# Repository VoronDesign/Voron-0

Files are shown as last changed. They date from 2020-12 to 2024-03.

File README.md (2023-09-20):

# Voron Zero

[**DOWNLOAD**](https://github.com/VoronDesign/Voron-0/archive/refs/heads/Voron0.2r1.zip)

Image of Voron Zero

The official release of the Voron Zero 3D printer. You can find the BOM in the configurator located at the [Voron Design]( http://vorondesign.com/voron0.2) website.

The current revision is **V0.2r1**

[**Printed Parts Guide**](https://docs.google.com/spreadsheets/d/1MSgTiXazJwyfcTe7QqNIMWwQ_lfM8cOXmiMWPZ2HkEI/copy)

## Highlights
- Compact and portable
- 120x120x120 build volume
- CoreXY
- Low mass direct drive extruder
- Enclosed chamber
- 24v DC bed
- Klipper firmware
- Filament runout sensor

## Release History

### V0.2r1 (2023 June)

**Skirts**
- We fixed the issue where 34mm Z motors didnt fit in the machine with the bottom panel installed, this involved increasing the height of the skirts/feet by 2mm
- We added a simple filament runout sensor to the rear right foot

**Toolhead**
- Mini Stealthburner direct drive and bowden cowling part cooling ducts improved 
- an issue with the guidler being able to pivot in an undesired direction was addressed by tightening the bolt holes to reduce play
- RIDGA support for the bearings that come stock with the ridga kit has been added

**Tophat**
- cam locks for the tophat were changed to a simple hex key design

**Z Endstop**
- z endstop mount was beefed up to improve ridgidity 

**BOM Changes**

the BOM increased by the following items
- 2x m2x10 self tapping screw
- 1x MR85 bearing
- 1x Microswitch
- 1x ECAS04 Bowden Collet

### V0.2 (2023 January)

A majority of the printed parts have changed. The configurator will give you an idea of parts needed if you are upgrading from V0.1.

**Toolhead**
- New design: Mini Stealthburner
- Direct Drive Extruder with BMG gears and 20mm thick pancake motor with 10 tooth spur gear
- Improved part cooling ducts (fans are same as V0.1)
- Supports Revo VORON, Dragon, Dragonfly BMO, DropEffect XG, Creality Spider Pro

**Drive units**
- Motor screw count reduction
- Endstop removed for sensorless homing

**Frame**
- No changes

**Tophat**
- All panels have changed
- All side panels are identical
- Extrusion based tophat
- Hinged design
- Cam locks to secure tophat in place

**Panels/Clips**
- All panels are 3mm
- Deck panel changed, new panel is not required
- Split rear panel

**X/Y Joints**
- Tops became 1mm smaller to accommodate MiniSB
- Endstop block removed for sensorless homing

**Bed Assembly**
- Printed parts changed, bed position moved 3mm to the rear

**Feet/Skirts**
- Trident skirt community mod folded into official release

**Front Idlers**
- Cam locks added

### V0.1 Inital release (2021 April)
See https://github.com/VoronDesign/Voron-0/releases/tag/V0.1

### V0.0 Updates and fixes (2020 Sept)
See https://github.com/VoronDesign/Voron-0/releases/tag/V0.0r1

### V0.0 Initial release (2020 April)
See https://github.com/VoronDesign/Voron-0/releases/tag/V0.0

Voron Logo

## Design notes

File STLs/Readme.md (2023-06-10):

You can Download the entire STL folder at once by clicking [**HERE**](https://download-directory.github.io/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)

# [Printed Parts Guide](https://docs.google.com/spreadsheets/d/1MSgTiXazJwyfcTe7QqNIMWwQ_lfM8cOXmiMWPZ2HkEI/copy)

This document lists all of the printed parts with images, names, and where they are used in the assembly manual as well as other helpful notes

# Part File Naming Guide

**QUANTITY REQUIRED**

*[a]_Thumb_Nut_x3.stl*  
Any file that ends with “_x#” is telling you the quantity of that part required to build the machine.

**BUILD SPECIFIC PARTS**

*SKR_E3_V3_Din_Mount.stl*  
Any file name that does **NOT** end with a quantity designation is a part that needs to be choosen based on the specific components and options you want for your build, things like controller boards, ADXL mounts or the Bowden toolhead are exampls of parts that will not have quantities and can be printed or not based on your choosing. 

**ACCENT COLOR**

*[a]_Tensioner_Knob_x2.stl*  
We have added “[a]” to the front of any STL file that is intended to be printed with accent color. The parts are marked with a heart in the manual when they first appear. 

**PRIMARY COLOR**

*B_Drive_Frame_Lower_x1.stl*  
These files will have nothing at the start of the filename.

**CLEAR / TRANSLUCENT**

*[c]_Display_Diffuser_x1.stl*  
Any file that begins with "[c]" is intended to be printed in a clear or translucent color that allows light to penetrate through it.

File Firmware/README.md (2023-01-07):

# Voron 0.1 Stock Printer Config Example

For detailed instructions on setting up your Voron, visit https://docs.vorondesign.com/build/startup/

As always, check Discord #voron_0_questions for help

## Quick Start

* Find and update your unique mcu `serial`
* Do a `STEPPER_BUZZ STEPPER=stepper_x` and repeat for each stepper
* Test each endstop using `QUERY_ENDSTOPS`
* Be ready to emergency stop, practice it
* Try homeing each axis, `G28 X` then `G28 X Y` then `G28`
* Adjust direction `dir_pin` as necessary
* Do a `BED_SCREWS_ADJUST` with the paper test
* Check fans are working properly
* Validate your thermistors `sensor_type`
* Tune bed `PID_CALIBRATE HEATER=heater_bed TARGET=100`
* Tune hotend with `M106 S64` then `PID_CALIBRATE HEATER=extruder TARGET=245`

## Warnings

* If using mainsail or others, you will likely need a special include or other adjustments
* You may need to swap your A/B motor physical connections and/or software stepper directions
* This firmware assumes stock BOM with Mini Stealthburner DD toolhead

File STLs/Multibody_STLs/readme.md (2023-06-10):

these Multibody STls are provided to make multi color printing of common parts such as the Cowling and skirts easier.

to use these STLs to print multi color parts import them into your slicer and split into parts (not objects) you can then use part specific settings to do things like color swaps or deleting top/bottom layer to make mesh skirts.

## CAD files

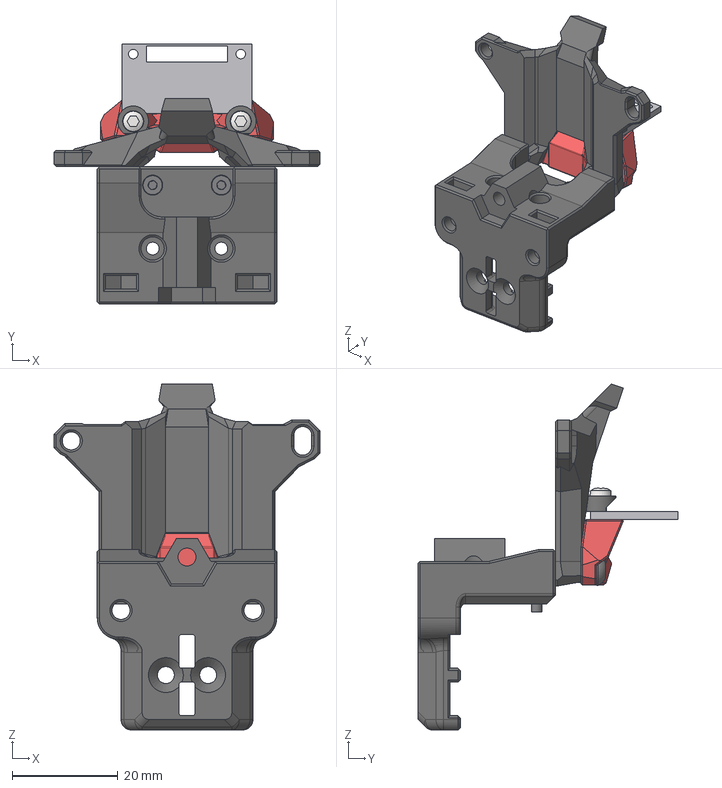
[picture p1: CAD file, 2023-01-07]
CAD/ADXL_Mounts/MiniSB_adxl_mount_adafruit_LIS3DH.step
50.3 x 49.2 x 65.5 mm
MiniSB_adxl_mount_adafruit_LIS3DH (1)
adxl_adafruit_LIS3DH
adxl_screw_spacer:1 (3) (1)
adxl_screw_spacer:2 (3) (1)
DIN EN ISO 7049 - ST2.2 x 6.5 - F - Z:1 (3)
DIN EN ISO 7049 - ST2.2 x 6.5 - F - Z:2 (3)
M3x12 BHCS (3)
X Carriage:1
Strain Relief Plate:1
M2x6 SHCS:2
M2x6 SHCS:3

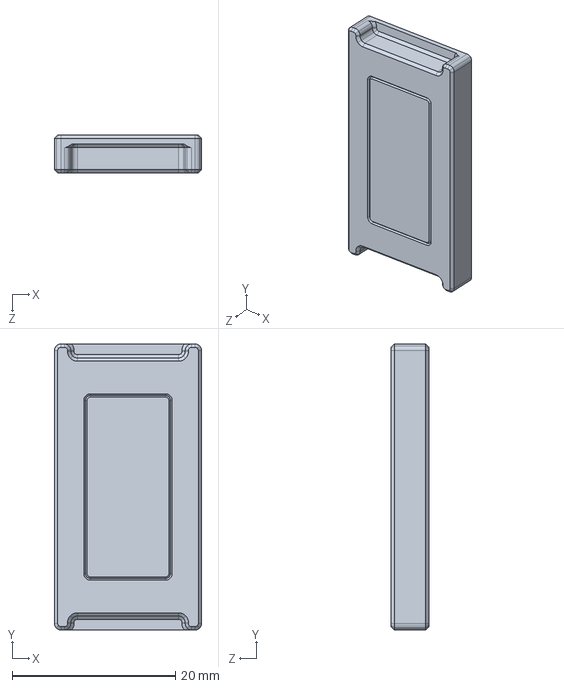
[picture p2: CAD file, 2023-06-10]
CAD/Electronics Mounts/VHB DIN Mount.STEP
18.0 x 35.0 x 4.60 mm

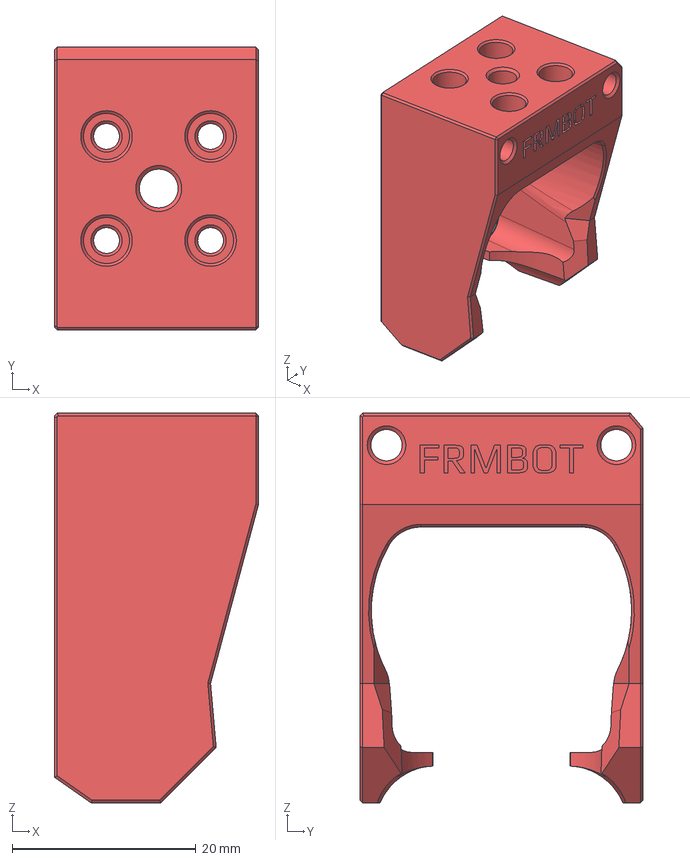
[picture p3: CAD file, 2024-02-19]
CAD/Hotend Mounts/Fan_Saver/FS_Hotend_Mount_Formbot.step
22.2 x 30.8 x 42.4 mm

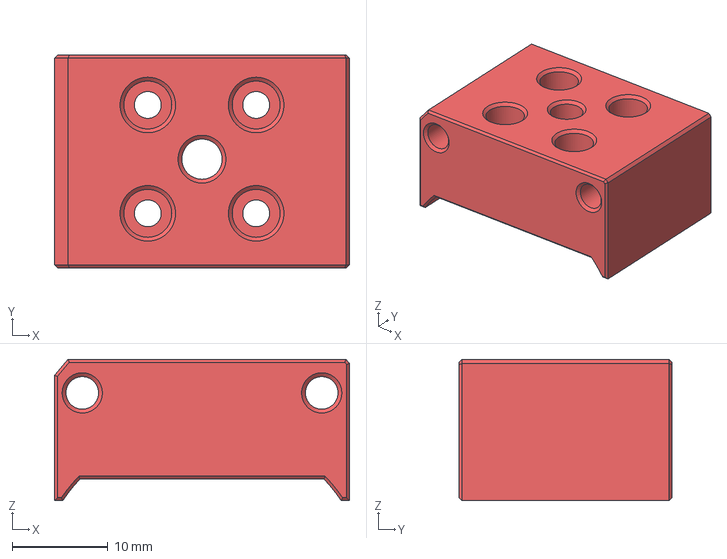
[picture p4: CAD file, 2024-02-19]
CAD/Hotend Mounts/Standard/Hotend_Mount_Formbot.step
30.8 x 22.2 x 14.7 mm

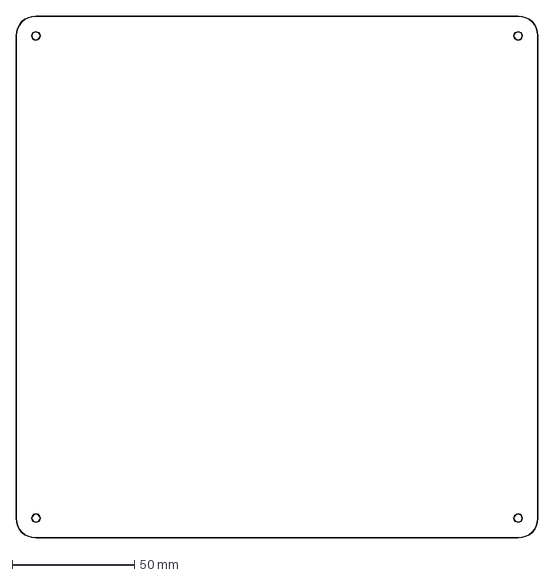
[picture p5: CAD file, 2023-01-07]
DXF/Bottom_Panel.dxf
213.0 x 213.0 mm

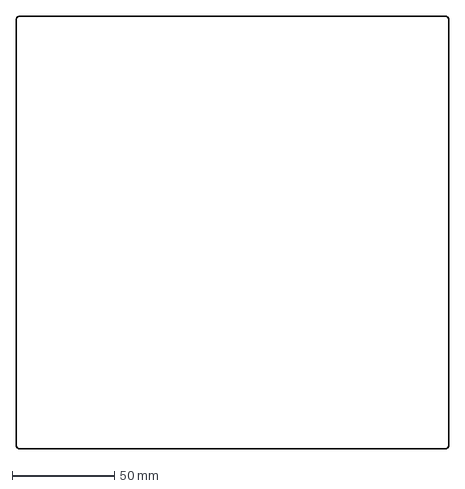
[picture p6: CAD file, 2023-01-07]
DXF/Tophat/Tophat_Top_Panel.dxf
212.0 x 212.0 mm

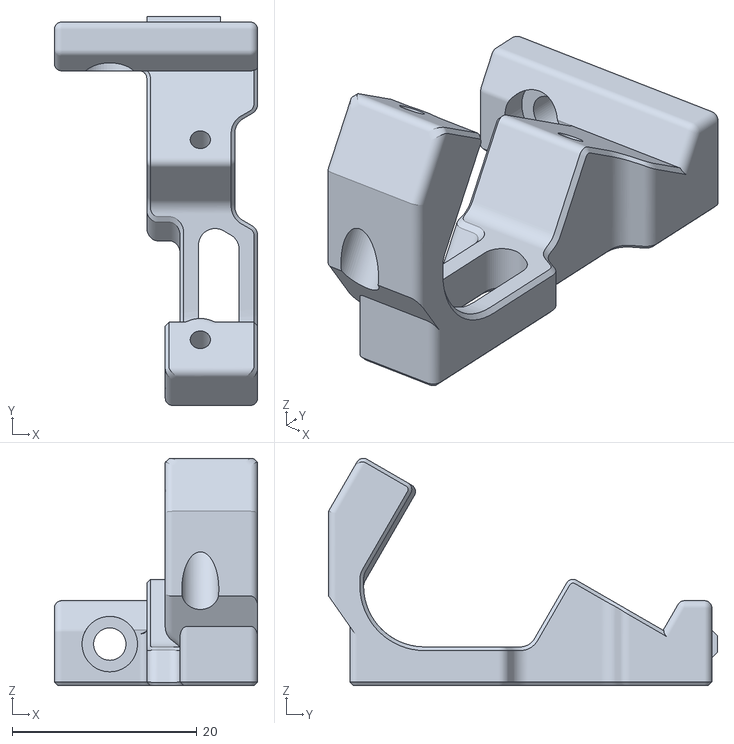
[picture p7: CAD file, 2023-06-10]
STLs/Display/Display_Mount_Right_x1.stl
22.0 x 42.1 x 24.6

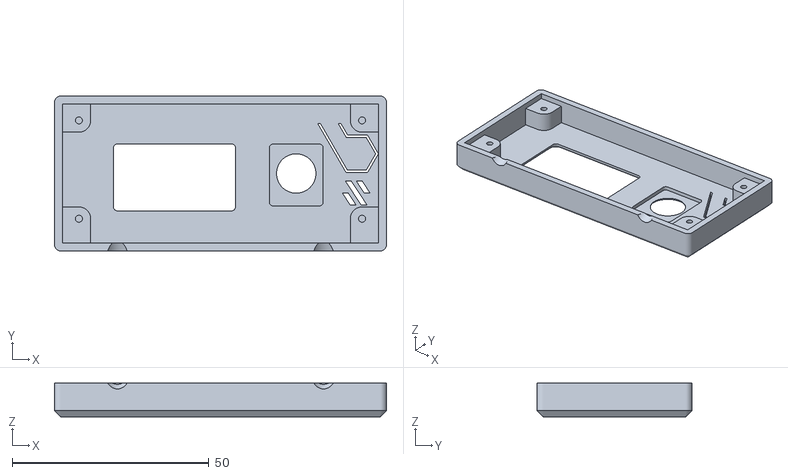
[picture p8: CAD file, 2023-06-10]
STLs/Multibody_STLs/Display/Display_Faceplate_Multibody_x1.stl
84.4 x 39.4 x 8.63

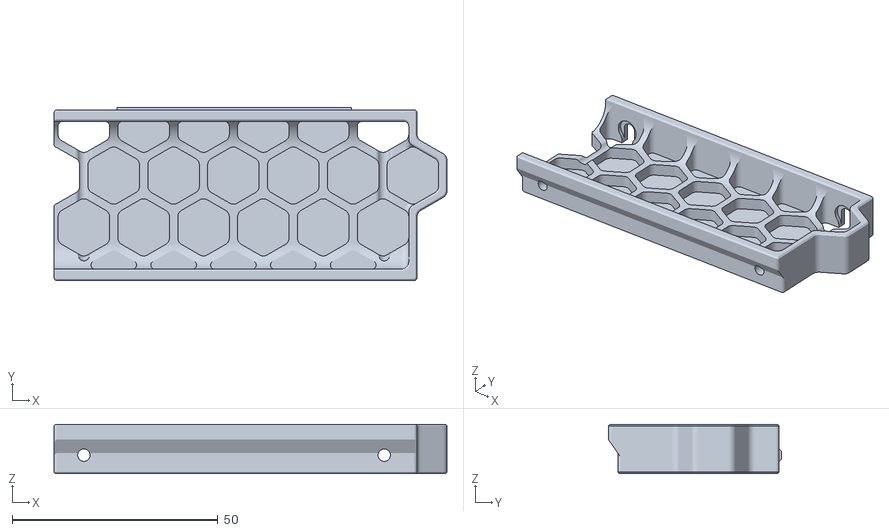
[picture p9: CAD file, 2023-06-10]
STLs/Multibody_STLs/Skirts/Side_Skirt_Mirror_Multibody_x2.stl
95.5 x 42.1 x 12.0

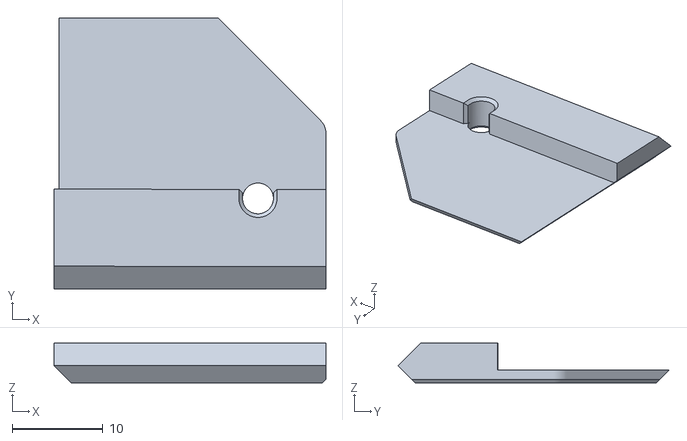
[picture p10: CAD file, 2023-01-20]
STLs/Panel_Mounting/Rear_Bottom_Left_Clip_x1.stl
30.0 x 29.9 x 4.40

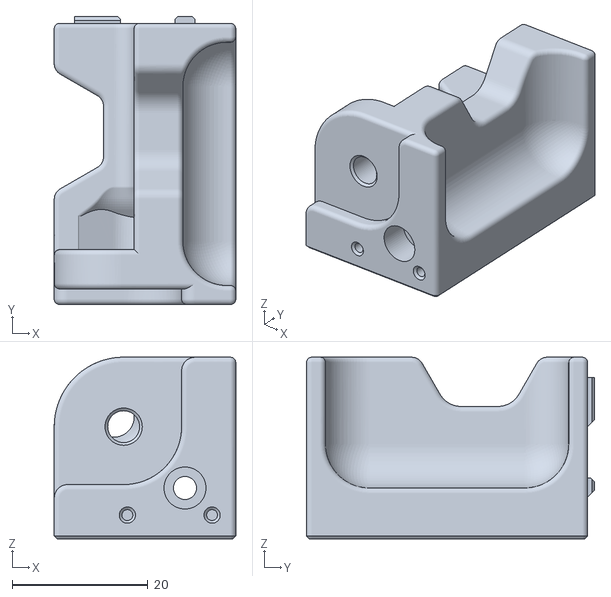
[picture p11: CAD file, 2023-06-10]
STLs/Skirts/Foot_Front_Right_x1.STL
26.8 x 42.5 x 26.8

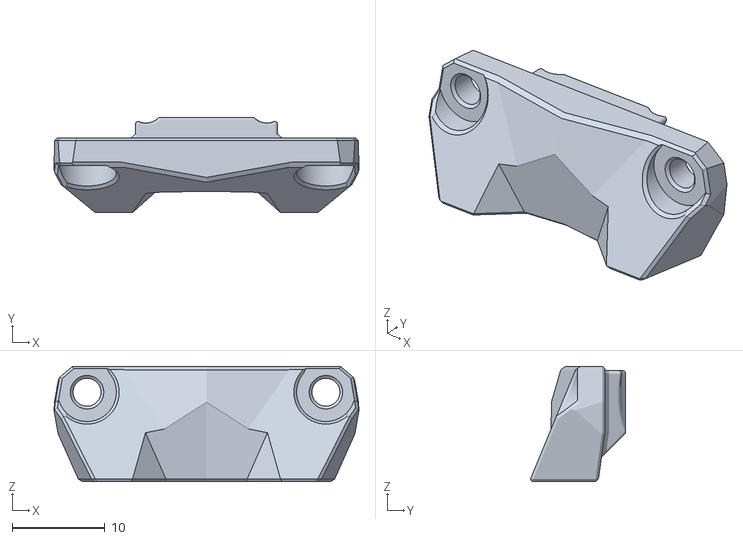
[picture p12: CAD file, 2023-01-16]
STLs/Toolheads/ADXL_Mounts/MiniSB_adxl_mount_generic_15.5mm.stl
32.8 x 10.3 x 12.4

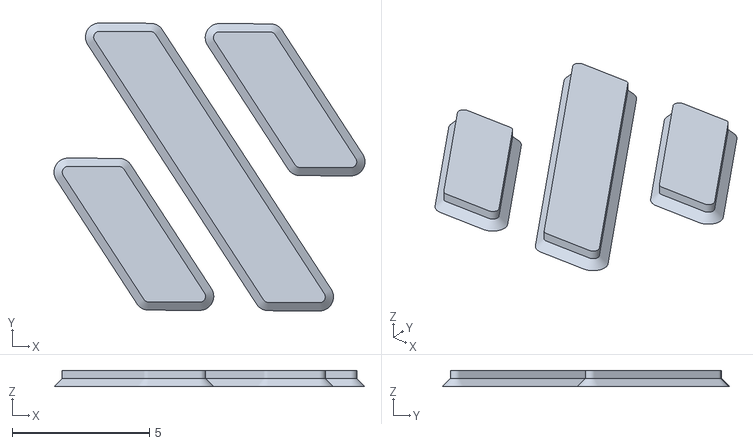
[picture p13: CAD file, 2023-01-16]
STLs/Toolheads/Bowden/MiniSB_Bowden_Logo_Insert.stl
11.3 x 10.5 x 0.6

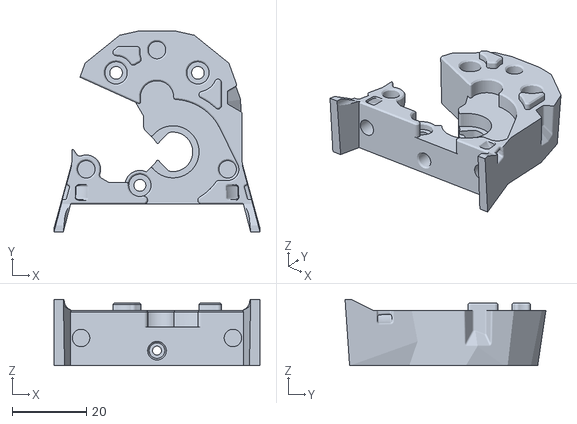
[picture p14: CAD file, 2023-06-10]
STLs/Toolheads/Mini_Stealthburner/[a]_MiniSB_MidBody_x1.STL
55.4 x 54.0 x 17.8

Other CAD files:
STLs/Electronics/VHB_DIN_Mount.STL
STLs/Toolheads/Hotend_Mounts/Fan_Saver/[a]_FS_Hotend_Mount_Formbot.stl
STLs/Toolheads/Hotend_Mounts/Standard/[a]_Hotend_Mount_Formbot.stl
STLs/Tools/Swiss_Army_Jig_x1.STL
CAD/ADXL_Mounts/MiniSB_adxl_mount_generic_15.5mm_c_c.step
CAD/ADXL_Mounts/MiniSB_adxl_mount_ldo_15mm_c_c.step
CAD/Electronics Mounts/Fly_Gemini_V2_Din_Mount_2pc.step
CAD/Electronics Mounts/Manta_M4P_Din_Mount_2pc.step
CAD/Electronics Mounts/RPi_or_BTT-Pico_Din_Mount.STEP
CAD/Electronics Mounts/SKR_3_Din_Mount.step
CAD/Electronics Mounts/SKR_3_EZ_Din_Mount.step
CAD/Hotend Mounts/Fan_Saver/FS_Hotend_Mount_Bambu_X1C.step
CAD/Hotend Mounts/Fan_Saver/FS_Hotend_Mount_Dragon.step
CAD/Hotend Mounts/Fan_Saver/FS_Hotend_Mount_Dragonfly_BMS_7_Fins.step
CAD/Hotend Mounts/Fan_Saver/FS_Hotend_Mount_Revo_Voron.step
CAD/Hotend Mounts/Standard/Hotend_Mount_Bambu_X1C.step
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

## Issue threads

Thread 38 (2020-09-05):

Gaps in Toolhead Blower Duct (Left)

mvrckcompany, 2020-09-05:
Thin walls around the screw holes on the part: "[a]_Toolhead_Blower_Duct_Left_TV6_x1" leads to gaps on the inside during slicing and printing. Attempted to alleviate the issue by enabling "Print Thin Walls" within Cura, to no avail.

Printed using recommended settings, please see attached for reference.

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

Roycinger, 2020-10-04:
I can confirm that S3D behaves in a similar fashion:
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

I'll have a try with SuperSlicer tomorrow

FHeilmann, 2020-10-19:
I checked back with the devs and they assured me that these holes do not impede the functionality of that part. Yes they are a little unsightly, but unfortunately the space around these featres does not permit a "fix" via thickening those sections.

I'm therefore going to close this issue. If you feel this has been in error and want to provide a rationale while this should be fixed apart from the visual aspect, feel free to reopen it!

Bests,
-Florian

FHeilmann, 2020-10-25:
@mvrckcompany the devs elected to fix your issue anyway. Latest master (with https://github.com/VoronDesign/Voron-0/pull/45 merged) should fix the slicing issue.

Closed 2020-10-19.

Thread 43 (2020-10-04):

Deck panel rear DXF missing segments

alatdneg, 2020-10-04:
I'm loading it into Freecad 0.18.4, and there are two curves missing, not sure if this is a FreeCAD bug or not, but the middle back plate loaded fine.

It's the two curves that connect the z-carriage inset.  --\\___/--

ta

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

Roycinger, 2020-10-04:
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

No issue for me here (QCad, Illustrator, Inkscape). Must be FreeCAD related

alatdneg, 2020-10-05:
Yup, FreeCAD seems to be a bit iffy on DXF's, I loaded it into Inkscape and re-exported as SVG, that loaded okay into FreeCAD.

I guess it might be nice if you included STLS of the plates at 3mm, 2.5mm  etc. As I imagine quite a few people would like to just print these, and it'd save them having to create the STL's from the DXF's which might be difficult for some people.

Closed 2020-10-05.

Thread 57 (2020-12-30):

Setup Guide Startup Pin No Serial Device

jgehrig, 2020-12-30:
The [Setup Guide](https://github.com/VoronDesign/Voron-0/blob/master/VORON-0/Manuals/V0_Setup_Guide.pdf) mentions setting `!PC13` on startup in the config. On my device with `!PC13` the serial port does not appear in `/dev` and no device is listed in `lsusb` either.

I resolved the issue above  by changing `!PC13` to `!PA14`. I suspect there was a hardware change in revision `V2.0`?

I'm not familiar with Klipper/SKR, and I can't find a good schematic to validate... Does this sound reasonable?

Upstream reference:
`https://github.com/KevinOConnor/klipper/issues/3461`

dubjay2k, 2020-12-30:
@jgehrig The SKR mini V2 does use a different pin than what's outlined in the setup guide (v1.2 specific).

It's mentioned in the V2 `printer.cfg` file, but should probably be mentioned in the setup guide as well.

https://github.com/VoronDesign/Voron-0/blob/74603b1752b24fcdebdb85c9d662b88075058e6f/VORON-0/Firmware/SKR_E3_Mini_2.0/printer.cfg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

raymondh2, 2021-02-12:
Closing due to inactivity

Closed 2021-02-12.

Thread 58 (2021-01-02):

Adjustment suggestions for the manual

Metti93, 2021-01-02:
Hello all
First of all I would like to say that I, a CAD designer, am very enthusiastic about this great printer. The parts, as well as the manuals and the community are of high quality and unparalleled.
That's why I want to use my skills as a quality manager and responsible for company standards in my company to make this great project even better. Starting with the manual!
When I assembled my V0, I felt a bit lost in certain parts of the manual.

**General hint:**
- That Loctite might react with ABS+ and might not be beneficial in certain places. A note on this might not be so bad, for noobs like me.
- I would make the text bubbles and their text larger. I'm not the youngest anymore, and would have liked more readable texts. Also, I'm not a fan of white text on an orange background.
- I would introduce a bubble/color for optional hints. Be it additional M3 nuts for future extensions etc..

**Page 6-7**
- I would number the profiles. Because I made the mistake of installing the wrong profile right at the beginning, which is what should be needed with the frame. Of course, I then simply added two holes. But that could have been avoided.

**Page 10-11**
- "2x" is not in the same place, on both sides!!!!! 😉

**Page 15**
- Bottom left illustration. Write on, nevertheless, please, that one puts a M3 nut under there in each case. I had wondered what it is held by, or if on any other pages this screw is used for something else, because it sits there loosely.

**Page 15-16**
- As an optional note, I would add additional M3 nuts lined with foam tape (thanks Christoph Müller#3576 for the tip).
Anyway, I would be happy if I had received such a tip early enough, and not only when I have assembled everything.

**Page 20**
- The title of the page is not aligned correctly.

**Page 25**
- A hint as to where the motor cable should look would be nice.

**Page 27**
- Backlash nut should be written on. Only at the end of the assembly, did I notice that this was missing. This was probably the worst thing missing from the manual.

**Page 29**
- Illustration at top left, "M3*6 BHCS + M3 Groove." Not that people use MakerBeam T-Nuts.

**Page 30**
- Foam tape would hold the nuts in place here, making it easier to mount the Z-motormount, but also the backpanel.

**Page 34**
- "M3*6 BHCS + M3 Nut."

**Page 35-36**
- M3 nuts, secured with foam tape, for future upgrades.

**Page 37**
- A measurement with the edge distance would be helpful, not that you tighten the rail in the completely wrong place already.
- Text "Use Rail Guides to Center Rail" is missing.

**Page 74**
- The M3 nuts on both sides of the rail should be listed, noticed they were missing on page 81. Had to take everything apart again.

**Page 136-137**
- The cable routing for the front fan, I would draw in better and route it through the notch for the left part fan.

For questions I am also available in Discord
All in all, it was fun to assemble the Voron.

mysfiring, 2021-01-15:
Didn't want to make a separate issue for a manual-related item: a callout on pg. 10 of the Pocketwatch manual - as a reminder to those using a non-spec motor - reminding the user that they should attach the 'pw_motor_spacer' at this point would be greatly appreciated! :D

nemgrea, 2021-02-20:
manual is getting re-made for v0.1 these issues will be taken into consideration and implemented where applicable

Closed 2021-02-20.

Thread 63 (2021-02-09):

Dragon Hotend Mounting

SneakyTiki, 2021-02-09:
The screws in the CAD are modeled as M2.5 x 12mm, but the stock Dragon Hotend (at least from Phaetus) comes with M2.5x8mm. The V0 BOM doesn't call for M2.5x12mm screws, and the Toolhead holes for mounting the hotend have 9mm of through depth :(

KoeRt888, 2021-02-09:
BOM calls for a V6 hotend, and I guess it only shows the BOM for this variant.
[Sourcing guide](https://vorondesign.com/sourcing_guide?model=V0) shows all hotend variants and contains the mention of the correct screws for the Dragon hotend.

raymondh2, 2021-02-10:
This is noted on the sourcing guide.

Closed 2021-02-10.

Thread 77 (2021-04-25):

BOM discrepancy?

bogeyf14, 2021-04-25:
BOM calls for "Bondtech Motor Gear" but it is unnecessary because the spec'd stepper already has a gear

VinnyCordeiro, 2021-04-25:
It is still necessary for those who opted for the bowden setup.

bogeyf14, 2021-04-25:
ok, I would recommend appending the description of that BOM line to say " Bondtech Motor Gear (required for bowden extruder)" or something to that effect. The manual doesn't show assembly of a bowden setup so it's not clear what this part is used for. I am sourcing parts for for the new toolhead and almost ordered this part because I didn't check the manual first, I doubt many other people will either.

raymondh2, 2021-04-25:
You are looking at two different versions of Voron zero

nemgrea, 2021-04-25:
issue fixed thanks for letting us know!

Closed 2021-04-25.

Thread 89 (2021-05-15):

Recommend revisions to V0.1 bed construction

fwiffo, 2021-05-15:
Having gone through a couple rebuilds of my bed, I'd like to offer a few suggestions for refinement:
1. Ditch the printed thumb knobs and go back to the knurled metal nuts from V0.0.
2. The Z adjustment screw hole strips out quickly. Thicker walls or something might help.
3. Put washers between the springs and lock nuts to keep them from getting cockeyed and buckling. I had a bad problem with mine shifting around on the nuts while adjusting. Adding a washer gave them a flat surface to push against.
4. Make the holes for the springs a bit shallower. That gives them a bit more tension at a given height making adjustments more reliable and gives a wider usable range.

nemgrea, 2021-05-20:
spec will stay with printed knobs for bom/cost reduction purposes. metal thumb nuts are still supported if users choose that route

im not sure what z adjustment holes would be stripping? we dont have any bolts threading into printed parts on z axis stuff

looking into adding the washers to help with the flat surface issue. this will require cad/manual updates

the hole depth for the springs is at its current depth to allow the full 120mm travel in z having the bed sit higher up may eat into this space. simply tightening the thumb nuts should compress the screw to whatever preload amount you would want. these parts will stay as modeled.

fwiffo, 2021-05-20:
I'm talking about the screw that hits the Z endstop switch (page 102 of the
manual).

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

--
Tom Schumm
http://www.fwiffo.com/

Megamannen, 2022-02-07:
Threading in plastic is really bad if you adjust it often. But I'm guessing this is a "set once or twice" for most users, in that regard it doesn't matter.

But the Voron is filled with threaded inserts, so what is one more?

staffert, 2022-02-09:
Simply using a second locknut would provide ample locking of the screw, or a brass heat insert with thread locking compound would be a better long term solution than simply a hole into plastic.

Closed 2022-08-04.

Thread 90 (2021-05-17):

20x5mm inlet fuse is missing from BOM

jarrettv, 2021-05-17:
These can be found at most hardware stores but it should be listed on BOM since you can't get going _safely_ without one.

DanJunior78, 2021-05-17:
Usually the inlets have a inlet fuse. Maybe a splitting between 220/110V heatbed to 24V power supply would make sense with 2 small 5A fuses

jarrettv, 2021-05-17:
I bought directly from digikey ala sourcing guide and it did not come with an inlet fuse.

DanJunior78, 2021-05-17:
Wow, usually they have a fuse coming with them. That's a usual size for inlets, even with a switch with light bulb.

nemgrea, 2021-05-18:
added

Closed 2021-05-18.

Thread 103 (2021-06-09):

Zip ties missing from BOM

grmocg, 2021-06-09:
Assembly requires zip ties in various locations, but they're not included in the BOM.

... And since some of the parts require smaller zip-ties than people are likely to have (smaller than 4in/100mm, which are typically the smallest in normal zip-tie assortments), it is worth a call-out somewhere like the BOM/sourcing guide!

nemgrea, 2021-06-11:
zip ties added to sourcing guide, thanks

samtny, 2021-06-21:
FWIW upon encountering this issue I grabbed these: https://www.amazon.com/dp/B0826Z1RLK

The quality is ... okay (minor burrs here and there), and my caliper says they are indeed 1.8mm width as described for the product.

tawera, 2021-07-08:
A suggestion for improvement: making the zip tie mount points compatible with 2.5mm would make sourcing easier. At least where I am from, I've checked many Swedish suppliers, all have 2.5mm, none have 1.8mm. And, incidentally, the ones that came with the prusa kit I bought were 2.5.

tme.eu has 1233 SKUs for zip ties, only 3 of which are 1.8mm or less, so these are rare...

Megamannen, 2022-01-15:
> A suggestion for improvement: making the zip tie mount points compatible with 2.5mm would make sourcing easier. At least where I am from, I've checked many Swedish suppliers, all have 2.5mm, none have 1.8mm. And, incidentally, the ones that came with the prusa kit I bought were 2.5.
>
> tme.eu has 1233 SKUs for zip ties, only 3 of which are 1.8mm or less, so these are rare...

Yeah, 1.8 is indeed a rare thing, here you have one (the only?) supplier though https://www.electrokit.com/produkt/buntband-71mm-x-1-8mm-svarta-100-st-panduit/

raymondh2, 2022-04-01:
Added to the BOM

Closed 2022-04-01.

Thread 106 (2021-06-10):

Wire length for x endstop is very tight

grmocg, 2021-06-10:
When wiring the V0.1, the suggest length of 400mm for the wire of the x-endstop seems a bit tight. Adding something like 20mm made it much more comfortable. Would be great to see a slightly longer length suggested!

grmocg, 2021-06-11:
Mounting the SKR after running this set of wires would make the lengths more reliably correct too, I suspect!

Closed 2021-06-14.

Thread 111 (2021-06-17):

Firmware/printer.cfg needs run current changes, too high for OMC Z-axis motors

KurioHonoo, 2021-06-17:
```
[tmc2209 stepper_z]
uart_pin: PC11
tx_pin: PC10
uart_address: 1
interpolate: True
run_current: 0.37       # For V0.1 spec NEMA17 w/ integrated lead screw
hold_current: 0.35
sense_resistor: 0.110
stealthchop_threshold: 500
```
The `run_current: 037` is fine for the LDO-42STH25-1004CL200E 1.0A, but is over the 0.28A max for the OMC 17LS13-0404E-200G 0.4A

Perhaps having two different configs in `[tmc2209 stepper_z]`, with the OMC being commented out by default, but adding additional commenting to inform the user.

I've added an example below as well as included all of the current BOM motors and their currents in case that information was helpful or if you wanted to incorporate them as comments into the config.

```
[tmc2209 stepper_z]
uart_pin: PC11
tx_pin: PC10
uart_address: 1
interpolate: True
#run_current: 0.37       # For V0.1 spec NEMA17 LDO-42STH25-1004CL200E 1.0A
#hold_current: 0.35
run_current: 0.2         # For V0.1 spec NEMA17 OMC 17LS13-0404E-200G 0.4A
hold_current: 0.15
sense_resistor: 0.110
stealthchop_threshold: 500
```

[tmc2209 stepper_x], [tmc2209 stepper_y]
OMC 14HS20-1504S 1.5A
LDO N/A

[tmc2209 stepper_z]
OMC 17LS13-0404E-200G 0.4A
LDO-42STH25-1004CL200E  1.0A

[tmc2209 extruder]
OMC 14HR07-1004VRN 1.0A
LDO-36STH17-1004AH 1.0A

hyperphonic0, 2021-06-19:
If you were going to have both configurations, it should probably the OMC motor that is uncommented by default because:
- The lower current setting of the OMC motor avoids any potential damage to the LDO motor, but the same is not necessarily true the other way around.
- The OMC motor is the _recommended_ motor in the sourcing guide, the LDO motor is the '_alternative source_'.

KurioHonoo, 2021-06-20:
I originally was going to say OMC too. Good point on it being the recommended one.

samtny, 2021-06-23:
Agree, choose the reasonably lower current as the default. My OMC was running super hot (2nd degree burn hot) before I caught this just now.

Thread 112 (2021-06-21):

Panel mounting clip STLs: incorrect part depth?

samtny, 2021-06-21:
About half the "3mm" set of panel clips have 5mm depth and fit my 3mm panel nicely, including room for VHB tape. The other half have 4mm depth and as a result have an awkward fit, requiring either loose tension of screws or some "flexing" of the clip to meet the rail.

The list of parts in the "3mm" set that have 4mm (perhaps incorrect?) depth is:

- 3mm_Bottom_Corner_Side_mirror_x1.stl
- 3mm_Bottom_Corner_Side_x2.stl
- 3mm_Middle_Clip_x9.stl
- 3mm_Top_Corner_Rear_mirror_x1.stl
- 3mm_Top_Corner_Rear_x1.stl
- 3mm_Top_Corner_Side_mirror_x1.stl
- 3mm_Top_Corner_Side_x2.stl

One way or the other, the fitment of the parts in this STL set seems to me inconsistent.

nemgrea, 2022-08-04:
this will be addressed with the v0.2 update

Closed 2022-08-04.

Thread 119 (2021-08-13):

Enclosing the high voltage compartment (bottom)

bmgoncu, 2021-08-13:
While the voron v0.1 is a great machine to tinker and build upon, there is a glaring safety issue of the exposed mains voltage compartment. The stock printer should include a solution where one can enclose the bottom with a 230mmx230mm acrylic sheet to keep fingers away whilst handling or moving the machine around.

For experienced users this may not be an issue but considering the popularity of this version  many novice tinkerers will build this printer.

nemgrea, 2021-08-16:
there are no exposed high voltage sources. psu terminals have a cover and all connections are spec'd to use correct fully insulated terminals. skirts also extend far enough down to prevent stray fingers from reaching the electrical cabinet.

it is never recommended to service or move the machine without first powering down the printer.

at the end of the day this is not a UL certified machine and it must be treated with a level of respect that any DIY mains voltage project would deserve.

Closed 2021-08-16.

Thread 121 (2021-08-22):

30mm blower fans sensitive to the hotend heat and stops working

bmgoncu, 2021-08-22:
The BOM specified GDSTime 30mm blower fans used for the Part cooling fans are susceptible to overheating from being in close proximity to the hotend.

Observed behaviour;
- When the hotend is hot the fan on the side of where the heater cartidge tip is visible, ossilates and doesnt spin
- When cooled down or when the hotend is not driven the fan spins as expected.
- The other part cooling fan spins normally.

Potential fixes;
- A not so temprature sensetive blower fan
- Somehow isolating the heat of the hotend from the fan hub.

Also asking for potential workarounds and/or solutions.

bmgoncu, 2021-08-23:
İ have done some further testing with a makeshift heat shield and it does appear to alleviate the problem. Havent tested with the chamber closed and heated but i think this is a good start;
https://youtube.com/shorts/RvsFIU7-kds?feature=share

https://youtu.be/qGwNJFiHI5k

bmgoncu, 2021-08-24:
Added the shielding with vhb to the fan (not ideal i know) the issue presides albeit the fan transitions to that state later (might be a placebo effect havent occured to measure the time).

bmgoncu, 2021-08-24:
More of the same issue i think;
https://discord.com/channels/460117602945990666/696930677161197640/877269535609212939

pfmooney, 2021-08-25:
Yep, I've seen this as well.  I even tried pushing the kickstart time up to 2s.  In a warm chamber, even 30% was too low for them to stay spinning sometimes, whereas 20% was fine cold.

pfmooney, 2021-08-28:
Al foil as a reflector does not appear to have helped at all.  I swapped the fan on one side for one of my spares and did not seem to help either.

lococnc, 2021-09-08:
Delta fans do not have this problem. My GDSTime fans lasted a day. Replaced and have no issues. Mine are 12v so it took adding a buck,

pfmooney, 2021-09-08:
> Delta fans do not have this problem. My GDSTime fans lasted a day. Replaced and have no issues. Mine are 12v so it took adding a buck,

That's for prints in a warm chamber, or in open air?

lococnc, 2021-09-08:
Sealed Chamber, printing ABS, I run fans 1t 16%

bmgoncu, 2021-09-08:
Can you provide an aliexpress link so i can verify? Maybe the BOM may change if it is indeed superior.

lococnc, 2021-09-08:
I bought from Digikey
https://www.digikey.com/en/products/detail/delta-electronics/BFB0312HA-A116/5022815
I used a small buck-converter to power the + terminal on fan, since the MCU switches ground.

blalor, 2021-09-08:
When talking fans, there’s little value in citing the brand or vendor as the sole detail. The DigiKey link is ideal. The useful info is in the specs, which are seldom provided on aliexpress, Amazon, etc. CFM, static pressure, voltage (obviously) and noise are all relevant.

lococnc, 2021-09-08:
Ali link to one identical to the ones I used.
https://www.aliexpress.com/item/1005003179503083.html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

Hexide, 2021-09-12:
Update on my insulation attempt:

After ~70 hours of printing, GDSTime fan started showing same failure symptoms. So issue was simply postponed rather than being fixed.

This calls for BOM fan to be changed to something that works better.

Personally, I will give a shot for listed Delta fan.

bmgoncu, 2021-09-12:
I already ordered a set, will arrive in 2 weeks i think. Will update with results.

xnaron, 2022-01-07:
@bmgoncu did the new fans work?  I noticed the Delta fan linked above is 12V.  Any issues with the airflow?  I guess it is better than a non spinning gdstime one :)

bmgoncu, 2022-01-07:
@xnaron yeah they totally do work, the airflow is signifocantly better (As it is the noise) and the best part no heat shielding at all (sorry for the radio scielence totally got carried away by other things and didnt report back)

xnaron, 2022-01-07:
@bmgoncu Awesome thanks!  Did you use a buck converter to get the 12V for them?

bmgoncu, 2022-01-07:
Actually no, i use the split wire config described in the doc

lococnc, 2022-01-08:
Buck it.

aschiweck, 2022-07-17:
> * Fan works fine when everything is cold
> * Fan maybe works for few layers if they are quick
> * Fan does not work by the end of print

I can confirm this issue also using a mosquito hotend.

I replaced the BOM specified GDSTime blower fans some time ago by ones from WINSINN, 30mm, Blower, 3010, Dual Ball Bearing, 24V. They are working smooth since then, regardless of heat or hotend state, no buck needed.

I bought them from [AmazonDE](https://www.amazon.de/gp/product/B08MKLDGQR/) but i think you can can get them also from https://winsinn.com/30mm-fan-raspberry-pi/ (3010 Blower - Dual Ball Bearing)

szafran81, 2022-12-10:
Both links from sourcing guide redirect to GDSTime fans (just checked).

Mstaniforth94, 2023-01-22:
I've recently been through about 6 of these fans, tried fan saver and this didn't help, and others on the Voron discord are still having issues with the fans on MiniSB.
https://discord.com/channels/460117602945990666/461210576618651669/1066792849221357578
Even with its new fan-saving design.

I have had one GDstine that's done 500+ hours and another do 20 minutes, 2 hours, 5 hours, 50 hours... on fully heat-soaked prints.

An inconsistent quality supplier is not a good quality one, with all the evidence and issues... I suggest these fans be removed from the BOM and the 5V Delta fans become the go-to. They may be double+ the price, but if that means you use less than double the fans over time, I think that's a better sourcing decision especially for newcomers just wanting to print stuff, and forcing the kit suppliers to send the better fans.

I did find cracking the door open stopped the issue on one of my GDstine fans, with fan saver too, but resulted in chamber temps cold enough to warp ASA on larger parts, thus meaning I was limited to ABS+ and small parts only.

szafran81, 2023-01-22:
My GDSTime did one Voron cube print, and after that they died each print after about 5mins.
Now I use the WINSINN 24V 3010 ones, and they work great.

porkcube, 2023-02-14:
Had GSTime 24V 3010 blowers on my 0.1, total failure of one in under 100hrs, replaced with Fabreeko upgrade kit and have almost 400hrs of them working fine since.

Separate new 0.2 build have been fighting the blowers, replaced right side 3 times before finally got a good cube out of ABS, then the left side started failing.   Tried fansaver and non-fansaver mounts which made no difference, only opening the door allows for a decent print with ABS.

Skystrike005, 2023-03-07:
I'm facing the same issue as well in miniSB. fan saver + dragonfly BMO lead to dead fans when the chamber is at printing temp. Fans are brand new, less than 1 hour of printing time.

Will try replacing the fans with winsinn ones. Heard they're much more stable. If all fails i'll try using dragon burner with 4010 fans.

nemgrea, 2023-03-16:
SG switched to winsinn fans mid feb. we'll try these for a bit. these are the fans i personally use in both v0's no failures yet.

danicedenv, 2023-03-20:
@nemgrea did you see any relevant dip in cooling performance? I ordered some Winsinn fans because my GDSTimes can't keep up with the heat. I am only hesitant because as far as I understand they don't push as much air and I mostly print PLA. Then again I don't want to give up being able to print ABS properly.

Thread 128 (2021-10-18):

Incorrect Stealthchop Setting in the Default Config

hyperphonic0, 2021-10-18:
There is quite a lot of discussion on Discord right now, with people having problems with the wrong default setting in the repo.  This has lead to many turning off Stealthchop entirely, meaning they will not benefit from near-silent - _and skip free_ - steppers.

[Klipper docs](https://www.klipper3d.org/TMC_Drivers.html) are fairly clear that Stealthchop should either be always on, or always off:

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

So I would suggest changing the default configuration for `stepper_x`, `stepper_y` and `stepper_z` to:

`stealthchop_threshold: 999999        # Comment out to turn off StealthChop`

I doubt that using Stealthchop on the extruder motor is going to provide any benefit, and because it can reduce the motor torque at higher speed it may cause problems. I would suggest turning it off for the extruder.

Stephan3, 2021-10-18:
https://github.com/Klipper3d/klipper/blob/5c10001bc525701f0ef004041cbbf093522f6de6/klippy/extras/tmc.py#L512

Take a look at the code. If value is 0, pwm mode is false and therefor the field in the register is too.
With a value of 0 stealtchop is disabled.

hyperphonic0, 2021-10-18:
I'm not quite sure what you're saying, but I'm suggesting the default config should have Stealthchop turned on by default, with the included comment explaining how Stealthchop can be turned off, if that is what is desired.

I believe setting `stealthchop_threshold: 0` would also turn it off, as would excluding the setting from the config.

samtny, 2021-10-21:
lol, i put a PR in for the extruder one, didn't see this issue:

https://github.com/VoronDesign/Voron-0/pull/127

#127

PR turns off stealthchop on the extruder only. I have personally troubleshot this with at least five people in the discord since I built my V0.1, July-ish.

hyperphonic0, 2021-11-02:
@nemgrea not sure why this was closed, #127 doesn't resolve this issue, it turns Stealthchop off for the extruder but does nothing the A/B drives or Z axis.

I think my original suggestion is still correct. I can create a pull request if you’d prefer, but thought an initial discussion here would be a better point of reference; It can be a bit difficult to discuss this kind of issue on Discord!

Closed 2021-10-31.

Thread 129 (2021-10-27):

Manual: Move mention of nut usage

newphreak, 2021-10-27:
On page 16 in the manual you're told to install the rail stoppers, but there's no mention of nuts being shown before page 18. Makes more sense to mention it the first place you use them. Props to setyte#5616 @ discord

HitLuca, 2022-12-30:
I also encountered this issue. A first timer may assume that they need to be screwed directly to the extrusion, which wouldn't be possible. Moving the note from page 18 to page 16 would easily fix the issue

Closed 2023-01-08.

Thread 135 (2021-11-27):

Problem in Downloading some .stl´s

klotzii-vr6, 2021-11-27:
There is a problem in downloading the following .stl´s:

- PSU_cover_x1.stl
- Power_Inlet_x1.stl
- Raspberry_Pi_3b_Mount_x1.stl
- Rear_Bed_Mount_Left_x1.stl
- Rear_Bed_Mount_Right_x1.stl

Can´t download them because after a click on the download button, it opens the file as a txt-file.
PSU_cover_x1.stl doesn´t even offer a download button

heizie, 2021-11-29:
try to use `git clone`

raymondh2, 2021-12-17:
Right click the text and save as.

raymondh2, 2021-12-17:
As for the ones without a download button click raw then do the same

Closed 2021-12-17.

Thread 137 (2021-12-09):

PrusaSlicer Profile extrusion width

gsezz, 2021-12-09:
The extrusion width percentages in the PrusaSlicer profile seem to be based on Nozzle diameter, like SuperSlicer does.
PrusaSlicer calculates them on Layer height.

raymondh2, 2021-12-18:
I'm not entirely sure what you are asking. Are you refering to the one build into Prusa Slicer? If so we don't maintain that.

gsezz, 2021-12-18:
No, I'm refering to the [VoronV0.ini](https://github.com/VoronDesign/Voron-0/blob/Voron0.1/Slicer_Profiles/PrusaSlicer/VoronV0.ini) here on github. For my Understanding, it's supposed to work with Prusa Slicer. But `extrusion_width = 110%` doesn't make much sense in Prusa Slicer, since it bases percentages on Layer height, not on Nozzle diameter, linke Super Slicer does. So while 110% sounds reasonable for Super Slicer (0.44mm extrusion width with a 0.4mm nozzle), this setting would lead to 0.22mm in Prusa Slicer (based on 0.2mm layer height).

nemgrea, 2022-01-05:
fixed

Closed 2022-01-05.

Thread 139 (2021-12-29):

5V Hot End Fan in to 24V FAN0

SanderRave, 2021-12-29:
Hi team,
I crossed this discrepancy by accident while searching for configuration info in Voron Documentation under Voron V0.0 - SKR mini E3 V2.0 Wiring: https://docs.vorondesign.com/build/electrical/v0_miniE3_v20_wiring.html#voron-v00---skr-mini-e3-v20-wiring

Bulit 4; Plug Hot End Fan in to FAN0 (pin PC6), is FAN1 (pin PC7) in the example Github printer.cfg: https://github.com/VoronDesign/Voron-0/commit/fa6f00e1f4592a6e5fb8976414297ccbbb6d4b64
Both pins have 24V output.

However, in the Voron sourcing guide, a 3007 axial fan 5V (min 3.5CFM) is specked: https://vorondesign.com/sourcing_guide
Connecting the fan straight to FAN0 or FAN1 will fry your hot end fan. With a lack of +5V outputs, my positive is wired to the probe +5V pin and FAN1 ground. Not sure where that wisdom came from, but I didn't make it up by myself.

Hope this helps making future building experiences even more awesome!

alvius, 2021-12-30:
You are looking at v0.0 documentation and v0.1 BOM. Check v0.0 BOM or v0.1 documentation.

raymondh2, 2021-12-30:
Closing as the referenced docs are not for the correct revision of Voron Zero

Closed 2021-12-30.

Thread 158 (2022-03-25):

Mosquito_Toolhead_DD for 3007 BOM fan

beaugalbraith, 2022-03-25:
Hey there,
Is it possible to create a MiniAfterburner toolhead for the Mosquito hotend using the 3007 fan? I printed the Mosquito toolhead. it appears to have been designed for use with a 25mm fan mounted directly to the heatsink. The other toolheads are designed for use with the 3007 fan seated inside the cowling.

If you look at the toolheads stls you can quickly see that the Mosquito version doesn't have the notch cutout, at the top, that the other toolheads have.

Thanks
-Beau

hyperphonic0, 2022-03-25:
Try this:

https://github.com/hyperphonic0/VoronMods/blob/main/V0.1_Mosquito_Cowling_with_3007_Fan.STL

raymondh2, 2022-03-25:
The toolhead is designed for the 2510 fan intentionally.

Closed 2022-03-25.

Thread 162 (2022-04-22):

Necessary part for bowden setup missing in V0.1 release

ianbruene, 2022-04-22:
The parts for a bowden toolhead are present, and the assembly manual does acknowledge that a bowden setup is possible even if it does not explain how to assemble it. However the belt retention block is not included in the V0.1 release. I had to dig up the previous V0.0 release to find the part.

If the bowden is deprecated to the point that parts can be dropped, then they all need to be dropped to avoid confusion. Alternatively if the option for a bowden setup is retained people need all of the parts for it.

Suggested fix: add belt retention block STL to the bowden toolhead directory.

nemgrea, 2022-04-22:
addressed by PR #163

Closed 2022-04-22.

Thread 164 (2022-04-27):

Manual: Change Z endstop trigger screw to SHCS from BHCS

Kozova1, 2022-04-27:
This screw on the T-nut block that is used for hitting the Z endstop is currently a BHCS.
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
It causes inconsistent endstop triggering and thus should be changed to be a slightly shorter (maybe M3x10?) SHCS screw.

raymondh2, 2022-04-27:
What do you mean inconsitent triggering? Between prints or when testing the endstop?

Kozova1, 2022-04-27:
Both - what happens is that sometimes I try to home and it crashes into the bed sometimes

nemgrea, 2022-08-04:
the screw is inline with the switch, changing to a larger hex head will cause more inconsistency as there is less contact area, refer to the cad for a better understanding of what im describing

Closed 2022-08-04.

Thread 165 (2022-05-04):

End of chain link attachment instructions is missing.

jbeougher7924, 2022-05-04:
Page 90 END LINK? WHAT END LINK?
The end piece of the chain was attached in an earlier step.
If you missed the installation you may be able to mount it to the outside.
A printed cable chain with a small bend radius is included in the released files

However on page 29 shows the end of chain is attached to the bed, however there are not instructions on how to do this.  Page 27 shows the same image but with out the chain link.  The instruction on page 90 are wrong since there is no instruction on attaching this to the bed.  Let alone that brass inserts are needed as well to attach the link to the bed.

ChrisN90, 2022-05-04:
It's not very clear in the manual but it is on page 13 under 'component prep'.

jbeougher7924, 2022-05-04:
Might want to clarify this page better and explain what needs to be done.  Align the page like the other pages.

Closed 2022-07-25.

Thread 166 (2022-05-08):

Manual: some issues I encountered on my build

atlaste, 2022-05-08:
First off, nice work! I really enjoyed assembling my machine using a PIF kit, and am eager to start printing with it. During assembly, I kept note of the issues I encountered, in the good spirit of open source sharing. I only encountered a few issues; hope it helps.

Issues I had with assembly:

1. Not really had an issue with this, but on page 59 it would be nice to say that the notches of the anti backlash nut should match up, so that they the nut stays on tension.
2. Page 64 should make a note about the rotation of the stepper. The kit I had (Fysetc) has the wires cut to the right length, so the connector for the cable should be pointed towards the back of the machine. This is a more general remark btw; I would have liked to know what the rotation was of the A/B stepper as well; during assembly I assumed the cables should go to the back instead of to the sides, which was wrong (and had to fix it later).
3. Screws that implicitly tap the plastic will destroy the plastic if it's not made to very tight tolerances. I found out the hard way while mounting the pcb brackets (crack...), and manually ran an m3 tap and a 1.5mm bit through the plastic to fix the issue (that's page 128 and 149).
4. Preload 4 nuts for the door handle magnet triangles. Page 38 I suppose, page 150 uses them. It's quite painful to add them later...
5. Belt tension on page 86 is hard to get right without some reference. Is it perhaps possible to use a phone and check the belt frequency?
6. Page 101 with the Z end stop. I just loosely put the nuts on the screws, and then fix them once they are in place. No need to drop them and fight gravity.
7. Page 108 apparently has a different PTFE length than I needed. I needed a total length of 30mm. I would perhaps note that the exact length is very important here; I cut it at 30.2mm at first, and to my surprise it was binding at page 114 because it was 0.2mm too long. It also seemed important to me to cut it with a sharp knife to ensure that the inner size is not smaller than it should be.
8. Getting those fans in place is terrible to get right... Pfew.
9. My thumb screw at page 116 has a separate spring which isn't noted. Feels quite tight. It does appear on the drawing.

That's it. As I said, nothing much for such a detailed design and manual. Hope it helps!

Cheers,
Stefan.

vavaroutsos, 2022-09-15:
I'll add a couple of more issues I had.

1) The lower cable chain end should be mounted to the extrusion using the top hole, not bottom. If you use the bottom hole, the top of the cable chain is a bit too high when the build plate is at Z=0 and it gets caught behind the gantry when moving towards Y=120.

2) The position in the manual for the Z guide rails seems at least 2mm too high. I had about 2mm of rail above the carriages when Z=0 (build plate thumb screws as tight as possible). This didn't allow me to get a full 120mm of Z travel.

3) The left/right position of the Z stage extrusions is critical for some build plates. The PEI spring steel I got with my LDO kit was slightly smaller than 120x120mm. This means any left/right shift in the build plate position (due to extrusion/rail location) takes away from usable build area. I lost a little over 1mm due to my build plate not being perfectly centered. This would not be an issue if the PEI spring steel were oversized 130x130mm.

HitLuca, 2022-12-30:
I took the feedback from @atlaste and updated the manual with some very simple annotations. @vavaroutsos , if you could give me the exact locations of the issues/tips you encountered I will update it with your suggestions as well.
I also added a note on which thread locker to use, as well as integrating the tip on cable routing from [this comment](https://github.com/VoronDesign/Voron-0/issues/176#issuecomment-1325972974)

Keep in mind it's a 5 minutes job and I hope it will be made obsolete by an update to the manual. I also had to compress it since the max file size is 25/26MB and the manual is 27 -.-

[Assembly_Manual_0.1_compressed.pdf](https://github.com/VoronDesign/Voron-0/files/10325070/Assembly_Manual_0.1_compressed.pdf)

vavaroutsos, 2022-12-30:
Referring to my previous comment:

1.	Page 36
2.	Page 18
3.	No page, probably an issue with the counter bore depth on the thicker LDO build plate.
4.	Page 25

Regards,

Pete

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

nemgrea, 2022-12-30:
we wont be making updates to the v0.1 manual anymore, we are focusing on the v0.2 manual which incorporates everything you have all mentioned here. thank you for the feedback.

HitLuca, 2022-12-30:
Well that's great news! Looking forward to see what the 0.2 improvements are :)

Anacardium12, 2022-12-30:
Is there already a known release date for the V0.2?

raymondh2, 2022-12-30:
There is no announced release date.

Closed 2023-01-08.

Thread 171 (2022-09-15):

BTT SKR mini E3 v2.0

vavaroutsos, 2022-09-15:
Can we remove this board from the sourcing guide/manual and replace it with something else? The SKR mini E3 v2.0 has no transient protection for the fan driver MOSFETs. The MOSFETs are rated at 30V which is easily exceeded by inductive switching spikes when the fan is turned off. This causes the body diode to go into avalanche break down. The MOSFETs are not designed to be operated this way and it's very poor practice. There are many threads on discord, reddit, github, etc. about fan failure on these boards.

The SKR mini E3 **v3.0** board has added flyback diodes to clamp spikes when switching inductive loads. The v3.0 board also has much better heat sinks and a 3rd fan output. The BTT SKR pico also has flyback diode protection for the three fan output MOSFETs, has a good heatsink, and is RPi form factor so it can be stacked..

nemgrea, 2022-09-18:
no further changes will be getting pushed for the v0.1 all efforts are now being placed on development for the v0.2 release which will not include the v2 skr board

Closed 2022-09-18.

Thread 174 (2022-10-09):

MidBody PTFE hole not deep enough.

paledrak, 2022-10-09:
It appears that on the STL for the [a]_Mid_Body_Revo_Voron_x1.stl has an error. The PTFE tube hole is only about 1mm deep and the PTFE tube does not sit securely in the Mid Body. The other tool head mid bodies have this hole much deeper.

It this by design or does the model need to be modified?

nemgrea, 2022-10-10:
this is by design, if the ptfe goes deep into BOTH the mid body AND the hotend then you will not beable to install the two components as the hotend needs to be installed and screws tightened before the mid body can be installed and it need to be slid into the assembly in a manor that would not allow 8mm of ptfe to be inserted at that stage.

so yes its done on purpose to aid in the assembly of the toolhead.

both the revo voron and the dragonfly BMO hotend require this smaller counterbore mid body.

Closed 2022-10-10.

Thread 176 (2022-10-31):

Manual Missing Critical Step

suprchunk, 2022-10-31:
Page 96 shows the installation of the cable chain. It shows the correct mounting for the top to the bed mount. It does not show it being attached to the bottom. It should show this. That is problem 1.

Problem 2: it doesn't mention shortening the chain to ensure that the y-stop isn't triggered/broken or whatever will happen when the bed is raised an one is no longer able to zero the machine.

The cable chain is obviously in need of shortening, however one does not realize this until the machine is constructed already.

There is also a need to rewrite the manual, as a lot of information is missing, not touched on, or somehow assumed. Just mentioning this one issue that I ran into that causes a serious issue; unless blocking a stop, or setting it off prematurely is intended.

nemgrea, 2022-11-01:
installation of the other end is shown on page 36.

the length of your chain depends on the supplier that you buy that item from. we will consider adding a note to the next revision.

> as a lot of information is missing, not touched on, or somehow assumed

if you have specific things you struggled with that would be helpful...general statements like this dont do us much good though if we dont know whats missing we dont know what to add...

eadz, 2022-11-24:
Personally I found the manual was a bit of an IQ test with puzzles to fill in the missing information in places.

Two things I did wrong, that were not explicitly mentioned in the manual:

Orientation of the plug for the A B motors  - the diagrams do not show this anywhere. Turns out the plugs need to face inwards. I had to redo this part.

The second thing is the wiring of the hot end wires, and how they go down through the gap between the z rails before going under the mentioned side gap. on page 91 there are two highlighted cable paths, but I believe that the cables also need to run through the gap at the back of the head bed?

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

Overall though, a pretty fantastic achievement to make a manual that can build a complex printer with an Ikea-style manual!

Closed 2023-01-08.

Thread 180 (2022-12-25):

Shift layers problem help

sima35, 2022-12-25:
Good, I have one problem ,that I can't solve even after several settings.
I set mechanically and klipper.
The problem is that for an unclear reason, the layer is moved.
The belt is stretched accurately.
Speed from 50-100, I don't use a higher speed.
I have it set stealthchop_threshold: 999999. I had it set to 250 and it was even worse.
I have the printer settings below.
Thanks in advance for all the help

[stepper_x]
step_pin: PC0
dir_pin: PC1
enable_pin: !PA8
rotation_distance: 40
microsteps: 16
full_steps_per_rotation: 200
endstop_pin: ^PB4
position_endstop: 120
position_max: 120
homing_speed: 85

[tmc2209 stepper_x]
uart_pin: PA3
tx_pin: PA2
uart_address: 0
run_current: 0.850
hold_current: 0.770
stealthchop_threshold: 999999

[stepper_y]
step_pin: PC14
dir_pin: PC13
enable_pin: !PC15
rotation_distance: 40
microsteps: 16
full_steps_per_rotation: 200
endstop_pin: ^PC8
position_endstop: 120
position_max: 120
homing_speed: 85
homing_retract_dist: 5
homing_positive_dir: true

[tmc2209 stepper_y]
uart_pin: PA3
tx_pin: PA2
uart_address: 2
run_current: 0.850
hold_current: 0.770
stealthchop_threshold: 999999

[stepper_z]
step_pin: PB9
dir_pin: !PB8
enable_pin: !PC2
rotation_distance: 8
microsteps: 16
full_steps_per_rotation: 200
endstop_pin: ^PB1
#position_endstop: 0
position_max: 120
position_min: -0.290

[tmc2209 stepper_z]
uart_pin: PA3
tx_pin: PA2
uart_address: 1
run_current: 0.350
hold_current: 0.300
stealthchop_threshold: 5

[extruder]
step_pin: PB2
dir_pin: PA15
enable_pin: !PD2
rotation_distance: 4.333
microsteps: 16
full_steps_per_rotation: 200
nozzle_diameter: 0.400
filament_diameter: 1.750
heater_pin: PC6
sensor_type: EPCOS 100K B57560G104F
sensor_pin: PC4
#control: pid
#pid_kp: 21.527
#pid_ki: 1.063
#pid_kd: 108.982
min_temp: 0
max_temp: 270

[tmc2209 extruder]
uart_pin: PA3
tx_pin: PA2
uart_address: 3
run_current: 0.320
hold_current: 0.280
stealthchop_threshold: 5

[heater_bed]
heater_pin: PC7
sensor_type: EPCOS 100K B57560G104F
sensor_pin: PC5
#control: pid
#pid_kp: 54.027
#pid_ki: 0.770
#pid_kd: 948.182
min_temp: 0
max_temp: 115

#fan for printed model FAN0
[fan]
pin: PA14

#fan for hotend FAN1
[heater_fan my_nozzle_fan]
pin: PA13

[temperature_sensor raspberry_pi]
sensor_type: temperature_host
min_temp: 10
max_temp: 100

#[temperature_sensor mcu_temp]
#sensor_type: temperature_mcu
#min_temp: 10
#max_temp: 100

[printer]
kinematics: corexy
max_velocity: 200
max_accel: 2100
max_z_velocity: 5
max_z_accel: 100

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

raymondh2, 2022-12-25:
Hello! We primary use GitHub for managing design issues and not printer support. I would recommend seeking support on our other platforms listed below.

Reddit: https://www.reddit.com/r/vorondesign/
Discord: https://discord.gg/voron
Forum: https://forum.vorondesign.com/

Closed 2022-12-25.

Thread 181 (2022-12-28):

[temperature_sensor mcu_temp]

sima35, 2022-12-28:
Can you help me, I have a temp problem for mcu in klipper.
If I approve the code for mcu temp in klipper it shows an error.
MCU 'mcu' error during config: Not a valid ADC pin
Once the underlying issue is corrected, use the
"FIRMWARE_RESTART" command to reset the firmware, reload the
config, and restart the host software.
Error configuring printer

sensor_type: temperature_mcu
min_temp: 0
max_temp: 100

timmit99, 2022-12-28:
For issues like this please use the Discord. Github issues for issues with the  files shown here.

Closed 2022-12-28.

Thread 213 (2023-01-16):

Why is there no support for the Mosquito hotend?

green-forg, 2023-01-16:
Just simply out of curiosity, why there is no support for the Mosquito hotend? Is this because of mechanical issues or something else? Sincerely look forward to any replay, and appreciate your guys' contribution.

nemgrea, 2023-01-16:
because i didnt want to make a mount for it.
I have no idea if it works or has issues as it was never tested with the new toolhead by the dev team.
the cad is available so anyone is free to make their own mosquito mount.

hyperphonic0, 2023-01-16:
@green-forg Here you go, it works great (so far) on the Mini Stealthburner.
Use the longer 2.5mm fan screws through the face with 'Mosquito' written on it for added stability.

[Hotend_Mount_Mosquito.stl.zip](https://github.com/VoronDesign/Voron-0/files/10427937/Hotend_Mount_Mosquito.stl.zip)

green-forg, 2023-01-17:
Wow! That's nice! Thank you for your replay!

Closed 2023-01-16.

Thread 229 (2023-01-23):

CAD different to STL's

MugenMicko, 2023-01-23:
Hotend Mounts don't have air ducting attached as per the CAD. Also, there is a fitment issue between the CAD Hotend mount with ducting and fitment to the Front Cowling. May need CAD updating

nemgrea, 2023-01-23:
hotend mounts with the "air ducting" are under the fansaver folder.

can you elaborate on what the fitment issue you are seeing in CAD is please?

MugenMicko, 2023-01-24:
I apologise, appears to have been rectified with a previous CAD update, my bad.

Closed 2023-01-24.

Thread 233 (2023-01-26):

Assembly Manual Correction

meistertek, 2023-01-26:
Page 27 Assembly Balloon "Preload 2 M3 Nuts" needs to be re-worded (Preload 4 M3 Nuts and screws) and needs a second circle end leader (multi-leader) pointing to the middle of the Top Extrusion. This will prevent people from missing that a total of 4 M3 Nuts are needed in this sub-assembly.

nemgrea, 2023-01-26:
i dont believe there are any other components that get added to that extrusion?

the preload nuts currently being referenced are for the Z_Motor_Mount to attach to

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

nemgrea, 2023-02-08:
Closing due to no response

Closed 2023-02-08.

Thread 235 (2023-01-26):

Rapido

Rajonex, 2023-01-26:
Hello,

What is the reason why Rapido mount is missing, but MicroSwiss hotend is included? I think it's not too big hotend, also quite lightweight with high flow. What for fun projects of Voron 0 prepared and polished to print with high speeds (300+) could be very beneficial. Am I missing some information about that? Or is it limitation of time of creator, what I totally understand. This project is awesome even without this detail.

Best regards

nemgrea, 2023-01-27:
it requires modification to the cowling.
user mod has been created here. you will also lose 3mm of z travel compared to stock miniSB
https://github.com/VoronDesign/VoronUsers/tree/master/printer_mods/Maverick/MiniSB_Rapido

Closed 2023-01-27.

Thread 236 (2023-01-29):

Link on page 144 points to the wrong video

fex42, 2023-01-29:
On page 144 in the assembly manual (magnet application on the build plate), the video link (https://voron.link/6zt4xt0) points to the wrong video (shows anti backlash T-Nut installation).

Maybe this video of Nero 3D is a better link (it explains not only the magnet but the whole build plate installation): https://www.youtube.com/watch?v=vZx4vfevwx4

nemgrea, 2023-01-30:
the link in the current manual in the repo points to the correct video

Closed 2023-01-30.

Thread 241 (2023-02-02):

Wrong hole size on SKR Mini E3 mount

YungChin95, 2023-02-02:
The SKR_E3_V3_Din_Mount.STL has 1.9mm holes for M2 self tappers, while the board uses M3 screws. 0.1 had the correct hole sizing.

nemgrea, 2023-02-09:
fixed https://github.com/VoronDesign/Voron-0/pull/246

Closed 2023-02-09.

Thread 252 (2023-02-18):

Manual: Page 53: wrong number of preload nuts

Dreistein75, 2023-02-18:
I just rebuilt my V0.1 to a V0.2 (all except the new TopHat, because no new hardware).
In one of the last build steps I wanted to wire everything and when I wanted to mount the 24V-to-5V-converter as it used to be for the V0.1 there were no nuts preloaded for this.
First I thought this will be an easy fix, but it turns out that you actually have to disassemble the whole frame to preload those nuts. This is very very bad user experience.
**Please** save others from this pain and mention additional 2 nuts on page 53 if you need to install a voltage-converter (like all people upgrading from an existing V0.1??)

nemgrea, 2023-03-03:
fixed
https://github.com/VoronDesign/Voron-0/pull/259

Closed 2023-03-03.

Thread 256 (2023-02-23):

sensorless homing - firmware missing macro

justgook, 2023-02-23:
i just build voron 0.2, and started initial setup,[documentation](https://docs.vorondesign.com/build/startup/)  is nice, it even explains how to tune sensorless homing.. problem was that if home few times in row, printer starts grinding it self.. only later i found out that there is need for homing_override described in [other section](https://docs.vorondesign.com/community/howto/clee/sensorless_xy_homing.html#homing-macros)

it would be nice to include those macros in firmware examples (im using [skr pico](https://github.com/VoronDesign/Voron-0/blob/Voron0.2/Firmware/bigtreetech-skr-pico-v1.0.cfg)), as they (macros) is kind of required to make sensorless homing work properly.

numanair, 2023-02-25:
I am using these macros which are inspired by that doc.
```
[homing_override]
axes: xyz
gcode:
  {% set home_all = 'X' not in params and 'Y' not in params and 'Z' not in params %}

  {% if home_all or 'X' in params %}
    _HOME_X
  {% endif %}

  {% if home_all or 'Y' in params %}
    _HOME_Y
  {% endif %}

  {% if home_all or 'Z' in params %}
    _HOME_Z
  {% endif %}

[gcode_macro _HOME_X]
gcode:
  # Get settings
  {% set max_x = printer.configfile.config["stepper_x"]["position_max"]|float %}
  {% set homespeed = printer.configfile.config["stepper_x"]["homing_speed"]|float %}
  # Pause to ensure driver stall flag is clear (ms)
  G4 P2000
  # Home
  G28 X
  # Move away from edge to quiet motors
  G90
  G1 X{max_x - 5} F{homespeed * 60}

[gcode_macro _HOME_Y]
gcode:
  # Get settings
  {% set max_y = printer.configfile.config["stepper_y"]["position_max"]|float %}
  {% set homespeed = printer.configfile.config["stepper_y"]["homing_speed"]|float %}
  # Pause to ensure driver stall flag is clear (ms)
  G4 P2000
  # Home
  G28 Y
  # Move away from edge to quiet motors
  G90
  G1 Y{max_y - 5} F{homespeed * 60}

[gcode_macro _HOME_Z]
gcode:
    {% set max_z = printer.configfile.config["stepper_z"]["position_max"]|float %}
    {% set homespeed = printer.configfile.config["stepper_x"]["homing_speed"]|float %}
    G28 Z
    # Move away from endstop
    G90
    G1 Z{max_z - 5} F{homespeed * 60}
```

Closed 2023-03-27.

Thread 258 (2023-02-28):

Manual pg. 147 - Cable Chain for Bed Heater Wires

hamsanwich, 2023-02-28:
The Rear_Bed_Mount_Right.stl is missing the protrusion for end of the cable chain that is shown in the manual on page 147.
Without a printed spacer, the cable chain turn radius is too tight to bend back and down to the new location in the bottom panel.

nemgrea, 2023-02-28:
its installed on page 36

the part is located here
https://github.com/VoronDesign/Voron-0/blob/Voron0.2/STLs/Drag_Chain_Spacer_x1.stl

Closed 2023-02-28.

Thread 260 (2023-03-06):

Missing washers in BOM

martingim, 2023-03-06:
I think there are 8 washers missing from the BOM for the v0.2. It uses 8 washers more than the v0.1 to attach the A and B stepper motors. (page 73 and 79 in the v0.2 manual). But the number of washers in the BOM for the V0.1 and V0.2 are the same.

nemgrea, 2023-03-13:
there are 43 washers needed in the v0.2, the quantities in the BOM have been rounded up to whole numbers to prevent people from buying too few or being stuck if they have a deformed screw/washer. the increase from 35 to 43 was still covered by our listing of 50.

martingim, 2023-03-13:
When I look at the bom on the vorondesign.com website it still says 35 shim washers. Am I missing something?

nemgrea, 2023-03-13:
> When I look at the bom on the vorondesign.com website it still says 35 shim washers. Am I missing something?

this should be fixed now, sorry for my misunderstanding and thank you for the report!

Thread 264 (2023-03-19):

SRK E3 V3 Wiring Diagram shows wrong polarity for FANs

Gabbajoe, 2023-03-19:
On the VORON_V0.2_Assembly_Manual.pdf on Page 204 we have the diagram:
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

But If you compare it to the PIN out diagram of the board it is the other way see:
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

nemgrea, 2023-03-19:
you have an old version of the manual, current version is 2023-03-03 and this is not a current screenshot from that manual. the issue was fixed some time ago.

Closed 2023-03-19.

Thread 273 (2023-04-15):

Recommended OMC motor for Z axis doesn't fit into V0.2

kmarty, 2023-04-15:
Hi,
docs/sourcing guide states that Z motor has to be high up to 34mm, which is e.g. OMC 17E13S0404MB-200RS (stated in sourcing guide, including link to it).
But there's only 32.2mm clearance:
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

Therefore named OMC motor doesn't fit here:
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

As a temporary solution I printed modified feet without 2mm recess (which seems as exactly the missing 2mm).

nemgrea, 2023-06-07:
https://github.com/VoronDesign/Voron-0/pull/291

Closed 2023-06-07.

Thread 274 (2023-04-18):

V0.2 display mount can't be slid in like all other skirt parts.

tkalbitz, 2023-04-18:
First of all a big thank you :-)

To align the nuts to install the skirt is quit bothersome. The version for V0.2 is great because you can already screw in the screw into the nut, slide the skirt part in, because it is open on one side, and then continue to fasten the secure. This open side is missing for the display mount and would make the install a bit easier.

nemgrea, 2023-05-12:
after looking into this we've decided to keep the current installation method, this is due to the orientation that the parts print in. if a slot is added we feel there would be a higher failure rate due to the small surface area that is against the bed on the one side of the slot feature. and we'd like to avoid having to add printed features that need to be removed prior to assembly

Closed 2023-05-12.

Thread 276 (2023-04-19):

Simplified side panel installation: V0.2 manual / BOM prefer m3x10 BHCS instead m3x8 BHCS

tkalbitz, 2023-04-19:
When installing the side panels m3x8 BHCS are referenced in the manual. I attached an image, because explaining is hard ;-)

To install the panel according to the manual: hold the panel in place and attach the printed parts. The cumbersome part is that you have to align every nut manually, make sure that it is not sliding down again and screw  it in at the same time.

When installing the panels the easiest way is to rotate the printer so that the panel you are installing is laying on top of the printer. You don't need to hold it anymore. You can than align the nuts and they stay where you put them. The problem I'm facing is that m3x8 bhcs screws aren't gripping the nut anymore. The screw can't grab the nut because the nut is to deep in the Extrusion and the screw threat isn't reaching it.

The "fix" is to use m3x10 bhcs screws instead m3x8 bhcs, which would be an huge simplification and improvement for the panel installation.

In the attached image you see, the described orientation of the printer,  on the left a m3x8 bhcs screw, on the right a m3x10 bhcs screw. Both screws are threaded the tiniest amount in an nut.

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

tkalbitz, 2023-04-19:
Just a shower thought: Why not have different "game modes" or "achievements" in a build. If you want to have a challenge use m3x8 and unlock "master of threads", if you want to enjoy the build (like a story in a single player game) use the m3x10 ;-) Thank you for the amazing work :-)

Closed 2023-04-20.

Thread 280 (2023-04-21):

CAD model missing 6 nuts on the X Gantry Extrusion

SrgntBallistic, 2023-04-21:
Was just looking through the CAD Model. I noticed when I hid the X Gantry extrusion to look at the preloaded nut locations that there weren't any nuts present to screw the X/Y Joints to the extrusion.

The instructions clearly shows pre loading the nuts but thought it could cause some confusion for anyone using the model as a reference for nut locations. Every other proloaded nut seems to be present
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

kyleisah, 2023-04-29:
Oops! I will take a look at this. Thanks @SrgntBallistic!

kyleisah, 2023-05-10:
Just want to provide an update. I've added the missing parts to the CAD. Just waiting on some other things to be finalized, and the newest CAD will be pushed. Thanks again!

SrgntBallistic, 2023-06-06:
@kyleisah I think I might have noticed a few more missing nuts.

The 4 for the door latch on the inside of the left front upright
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

SrgntBallistic, 2023-06-06:
I have only been able to note these things because I've created a barebones version of the Fusion file with just the extrusions and hardware to help myself (and maybe others) identify were all of the preloaded nuts are.

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

nemgrea, 2023-06-07:
https://github.com/VoronDesign/Voron-0/pull/291

Closed 2023-06-07.

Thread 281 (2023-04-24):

CAD / Real life collision of motor mount and strain relieve plate.

tkalbitz, 2023-04-24:
I was searching why I coudn't use all 120mm travel and found that the strain relief plate (I use the one from the V0-Umbilical  mod) collides with the screw hole offset face when homing. I see the same in the CAD model see screenshots). I removed the part with a knife and now homing works a lot better. Of course this could be an interaction between V0-Umbilical backplate and motor mount.
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

tkalbitz, 2023-04-24:
This is for sure related to https://github.com/VoronDesign/Voron-Hardware/issues/193

raymondh2, 2023-04-26:
This is not an issue with Voron Zero. This is a V0 Umbilical mod issue.

Closed 2023-04-26.

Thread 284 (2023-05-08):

Electronics STLs: VHB DIN mount and PCB DIN clip are incompatible

settinger, 2023-05-08:
In the current version of the repo, there is an STL file [`VHB_Din_Mount_x2.stl`](https://github.com/VoronDesign/Voron-0/blob/Voron0.2/STLs/Electronics/VHB_Din_Mount_x2.stl), which replaced an older STL file [`VHB_Din_Mount.stl`](https://github.com/VoronDesign/Voron-0/blob/d9e205dd984bb772386feaa3e9d27dadbdf73b85/STLs/Electronics/VHB_Din_Mount.stl), no longer in the repo.

The issue is that the current file [`PCB_DIN_Clip_x2.stl`](https://github.com/VoronDesign/Voron-0/blob/Voron0.2/STLs/Electronics/PCB_DIN_Clip_x2.stl) does NOT fit the current `VHB_Din_Mount_x2.stl`, but it DOES fit the older, deleted `VHB_Din_Mount.stl`. The angled cleat portion of `VHB_Din_Mount_x2.stl` is too thick, and the portion of `PCB_DIN_Clip_x2.stl` that is supposed to "snap" into place is unable to catch on anything.

If anyone else prints all three STLs and gives them a test-fit to confirm or contradict what I found, I'd greatly appreciate it! I don't *think* this is an issue with my printer tuning, but printers always have a way of surprising me, so who knows? :)

kyleisah, 2023-05-10:
Hey there! The DIN cleats were my idea. I designed them and tested them myself, and they've been released for a few months now.

But, to see if maybe something was wrong, I printed them again straight from the repo and they worked just fine.

Here's some photos, maybe you've got something upside down?

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

settinger, 2023-05-10:
Thanks for looking into it, and thank for designing the cleats in the first place! That's definitely the same cleat orientation that I was using. I've attached a video of clip and the cleat that I printed yesterday, and how they pop apart with very little force. The original cleat, by comparison, is very secure; I'd film a demo of that part for you, but it's already sealed up in my V0 build, haha!

https://github.com/VoronDesign/Voron-0/assets/7494643/3a74da9c-3dba-4304-8ef0-3f05f025b772

Here's a cross-section of the old cleat (left) and current cleat (right). Perhaps they are just different enough that it only makes a difference on a less-well-calibrated printer like mine? If that's the case, I can see the argument for not needing to alter the design, but it's strange because the older version worked so, so well for me!

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

kyleisah, 2023-05-10:
I'm curious if what you're having is due to thin wall settings or something like that. It looks like your DIN clip is sort of rounded where there should be a small protrusion from the front leg.

Do you have a sliced gcode file of the PCB DIN clips and the current rev of the cleats?

If that something like that is due to a slicer issue, I definitely want to help improve it!

And thank you! KAMP is a lot of fun, and super useful. 😄

settinger, 2023-05-10:
Sure thing! [Here are the sliced gcode files for the clip and both cleats.](https://github.com/VoronDesign/Voron-0/files/11438028/VHB.DIN.gcodes.zip) These ones are printed in PLA, but the ABS ones I printed a few weeks ago have the same fitment. Which clip leg is the front leg you mentioned? I'll get some still images in the morning if that'll help.

kyleisah, 2023-05-20:
@settinger Hey, just getting back to this. I took a look at the gcode files you shared and compared them to mine, and they look the same. The pieces that I printed, I agree, could feel a bit better. They don't feel as strong as I think they should. I'll see if I can dig up some old files or just redesign a new clip. If you'd like, I can send an STL over to you for you to try?

kyleisah, 2023-05-20:
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
I think something like this could be kinda fun 😄

kyleisah, 2023-05-20:
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

These seem to clip a bit better and hold a bit better. But let me know please, so we can get them into the repo. 😄

[VHB_Din_Mount_Fix.stl.zip](https://github.com/VoronDesign/Voron-0/files/11521239/VHB_Din_Mount_Fix.stl.zip)

settinger, 2023-05-20:
Rad! I'm loading up my ABS now!

settinger, 2023-05-20:
Now _that_ is a secure clip! I printed all three VHB DIN clips in one go: the old one that worked for me previously, the one that's current in the repo, and your new one with the cool logo. Sure enough, the oldest one and the newest one lock in place perfectly. Thanks a ton for whipping that up, I hope some other folks can print these and chime in with their results as well!

dtdionne, 2023-09-17:
Hmmm, I have a similar issue.  It's like the backstop is almost a mm too thick or tall.  The cleat doesn't snap in.  I did the best I could trying to interpret voron print settings into orca slicer.  I haven't had this kinda trouble with any other parts and I printed all my own parts for the 0.2.

But i do think there's a "thin wall" check box.  I've already printed a dozen of these in different materials to test...what's a few more.

dtdionne, 2023-09-17:
I just watched that video and the ones I just printed don't even fit that good.  I shaved a little over .5mm off one and it snaps in now.  But mine cleat also seems more rounded where it should (and probably is) sharper.  I bet it's a print setting in orca.

Closed 2023-06-07.

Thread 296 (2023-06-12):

Voron0.2r1 - [a]_MiniSB_Cowling_x1 HE Fan face only 2 layers (0.4)

nigelpjames, 2023-06-12:
The front of the cowling around the HE fan appears to only be 2 layers thick (0.4)?  Seems too thin and wonder if this is an oversight/mistake?  In the previous release the front was 4 layers thick (0.8).

Layer 3 - New 0.2r1 on left, 0.2 on the right.  Issue also with multi-part cowl version

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

nemgrea, 2023-06-12:
the current STL's inm the repo are 3 layers thick. looks like you downloaded the files before the PR was fully merged, this has been fixed

nigelpjames, 2023-06-12:
no, i only downloaded the repo 12hrs ago from the default r1 branch.  the files are showing as PR #291 which doesn't mention  the fix and both cowls still appear to only have 2 layers

nemgrea, 2023-06-12:
Check your slicer settings the part thickness is 0.6

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

nigelpjames, 2023-06-12:
Thanks, all good now...slightly thicker first layer so much have been on the margin since its still thinner than the 0.8 in RC2

nemgrea, 2023-06-13:
V0.2 Master Assembly RC2.zip
this is not the cad file that appears in the github....

scul86, 2023-06-13:
Copied the wrong filename.

Reverified that I was using this file:
[V0.2R1 Master Assembly v62.step.zip](https://github.com/VoronDesign/Voron-0/blob/Voron0.2r1/CAD/V0.2R1%20Master%20Assembly%20v62.step.zip)

Closed 2023-06-12.

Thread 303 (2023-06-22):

Filament sensor foot for V0.2(R0) height

Kagee, 2023-06-22:
It would be very nice to have a (official) model for a V0.2R0 (2mm shorter) filament sensor foot in the repository. Either in the 0.2 or 0.2R1 branch. Because of how the height was increased, it is unfortunately not enough to just cut 2 mm from the bottom of the R1 foot.

driemekasten, 2023-08-16:
I modified the official frs foot to match the 2 mm shorter v0.2 feet and skirts.

PR can be found here:
https://github.com/VoronDesign/VoronUsers/pull/986

Closed 2023-12-05.

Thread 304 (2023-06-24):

Config - Sensorless Homing Current & Macro Confusion

SrgntBallistic, 2023-06-24:
I had some issues setting up Sensorless Homing for my Formbot V0.2(r0) Kit.

I used the [`bigtreetech-skr-pico-v1.0.cfg`](https://github.com/VoronDesign/Voron-0/blob/Voron0.2/Firmware/bigtreetech-skr-pico-v1.0.cfg)

While also walking through the Voron Docs Initial Startup guide and Klipper TMC Docs.

I first walked through all the instructions in the .cfg file.

I set the motor currents based on the recommended equation in the file.

["# you need to calculate the run_current value using the equation (rated_motor_current * 0.707 = Maximum_run_current) start with a value that is about 60%-70% of your maximum value."](https://github.com/VoronDesign/Voron-0/blob/a4d02db92a7dd71e8f2c72d6f74f6bc3b9d020c8/Firmware/bigtreetech-skr-pico-v1.0.cfg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)

My Moons motor currents are:
- A/B - 1.5A
- Z - 0.65A
- E - 1A

Using the above equation and factoring a 65% ( x0.65) starting value, I ended up with the following currents
- X/Y - .69
- Z - .3
- E - .46

When I got the the `_HOME_X/Y` macros I first found the wording a bit strange for changing the `XX` value. It states:

["{% set HOME_CURRENT = XX %} # replace the XX with a current value that is about 70% less than your run_current value for X and Y "](https://github.com/VoronDesign/Voron-0/blob/a4d02db92a7dd71e8f2c72d6f74f6bc3b9d020c8/Firmware/bigtreetech-skr-pico-v1.0.cfg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)

By 70% less does this mean to set XX to 30% of our calculated `run_current`? That's what I took it as.
.69 * 3 = .21 which is a very low current setting.

After doing so I had a lot of trouble getting a stable Stall Sensitivity as outlined in the Starting Guide.

Taking a look at the macro closer I noticed it's actually taking that XX value and setting it as the `HOME_CURRENT` value. But then sets the current to `HOME_CURRENT * RUN_CURRENT` for homing

So it seems to me that it is actually looking for a decimal percentage?

Looking at the macros presented in the [Voron Sensorless Guide](https://docs.vorondesign.com/community/howto/clee/sensorless_xy_homing.html) and the [Klipper TMC Sensorless Homing Macros](https://www.klipper3d.org/TMC_Drivers.html#using-macros-when-homing) section I noticed that neither do any multiplication. They just directly set the current to a hardcoded value for homing and change it back.

So it's possible I've just really confused myself here and read things wrong. Or is the intention to change the `XX` value to a percentage that will be multiplied by the `RUN_CURRENT` to drop the current during homing? Or lastly is the goal to have users manually set a current value that's lower than the set `RUN_CURRENT`?

kyleisah, 2023-06-26:
Hey there, just letting you know I will be taking a look into this and see if there's something better I can come up with that works for newbies and pros.

nemgrea, 2023-06-26:
https://github.com/VoronDesign/Voron-0/pull/305

SrgntBallistic, 2023-06-26:
> Hey there, just letting you know I will be taking a look into this and see if there's something better I can come up with that works for newbies and pros.

Thanks. I definitely saw a couple other folks in the discord channel having questions about that.

One of those things were ppl are likely figuring out what it means and how it works. But the clarity can just short circuit some of the process to get to a working value.

Thanks for the work! The config worked great to get started!

Closed 2023-06-26.

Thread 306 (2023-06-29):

Add clearance between hotend and x carriage

Matszwe02, 2023-06-29:
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

I have dragon hotend and my mini stealthburner is tilted a little because the hotend presses against the ends of the belts. I needed to trim these belts to be flush with x carriage and only then there was no issues with the stealthburner.

nemgrea, 2023-06-29:
this issue is addressed on page 142 of the assembly manual
`trim the belts
to their final lengths, the amount you can leave depends on the hotend you are using. If your hotend sits flush against the X carriages front facing surface a flush cut may be required.`

there is simple no extra room to add space for oversized heatsinks like those used on the dragon toolhead.

Matszwe02, 2023-06-29:
> there is simply no extra room to add space for oversized heatsinks like those used on the dragon toolhead.

And I think that's the issue: someone explained in voron's discord that textured pei can add the minimal amount to z height, which is sufficient to cause issues with the clearance. Maybe extend the z carriage or anything else by let's say 0.2 or 0.4mm so it will fit better?

nemgrea, 2023-06-29:
the toolhead will hit the front door if the x carriage is extended.

Matszwe02, 2023-06-29:
> the toolhead will hit the front door if the x carriage is extended.

ok, right. Is it possible to make some belt guides to fold away or there's just no way it can fit?

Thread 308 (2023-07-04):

Guidler has too much play - possible solution

Matszwe02, 2023-07-04:
Ministealthburner has an issue that the amount of play in the guidler is significant enough to cause issues when extruding. It could grab filament too weak for fast printing, and everything above 5mm³/s wasn't possible.

https://github.com/VoronDesign/Voron-0/assets/49353902/af5799f3-7e6b-418b-82b3-9f7547d47321

I made some changes on the guidler that will fix it - check it out.
I narrowed the bold hole from 3.2mm to 3.1mm (which is still enough for even less accurate printers) and applied a tiny angle to push it towards filament. In that way the remaining wobble that may still be there will be directed towards the filament, not away.

[V0.2 Guidler v1.f3d.zip](https://github.com/VoronDesign/Voron-0/files/11952082/V0.2.Guidler.v1.f3d.zip)

nemgrea, 2023-07-05:
Are you sure youre extruding at 5mm cubed per second and not just using the preset numbers in mainsail that are linear feed rates and not volumetric flow rates?
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

Matszwe02, 2023-07-05:
> Are you sure youre extruding at 5mm cubed per second and not just using the preset numbers in mainsail that are linear feed rates and not volumetric flow rates? 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

yes, I was looking at this parameter:
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

After this mod i'm no longer extruding max 5mm³/s, but I'm now maxing out the hotend at 15mm³/s. Further speeding up actually forces extruder motor to skip instead of gears grinding. I may later install cht nozzle, which will push these limits even more, but now I'm sure that the guidler doesn't cause any issues.

probably-Erwins-Cat, 2024-01-26:
Shameless commenting here that your issue might be mine in disguise: https://github.com/VoronDesign/Voron-0/issues/340.

Matszwe02, 2024-01-27:
> Shameless commenting here that your issue might be mine in disguise: #340.

My post is about bad tolerances that lead to too much play on the guidler (I never experienced thermal deformation, just the high amount of play that this part has), your post is about the temperature that is badly managed - so I think 1 part, 2 issues

nemgrea, 2024-04-30:
closing do to updated issue being submitted

Closed 2024-04-30.

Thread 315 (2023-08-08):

Distance between Lower Stain Relief Body Screws and Top A/B Mounts too small to account for compounding tolerances

ChaosBlades, 2023-08-08:
I noticed that the screw head is ever so slightly colliding with my top A/B motor mounts. I would hazard a guess this is the case for several people and they just have not noticed. I ended up taking a file to the top A/B mounts to make clearance. Compounding tolerances is the cause of this. Such as over sized M3 screw heads, linear rail heights, extrusion dimensions, and the print head slighting rocking back when it gets tightened due to again compounding tolerances in printed parts. This could cause inconsistent sensor less homing issues.

Lower Stain Relief Body screws should be raised by 1 mm to avoid this issue or could be raised by 0.5 mm and the top of the A/B motor mounts lowered by 0.5 mm.
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

nemgrea, 2023-08-08:
ISO 7380-1 tolerance for m3 screw heads is a max value of 5.7mm so the cad is already at the max material condition for the screw.

dimensional tolerances for MGN7 rail heights are at most +/-0.04mm (class C precision)

ChaosBlades, 2023-08-08:
My original V0 kit came screw heads of up to 5.95 mm I didn't use them for this though. My original rails were actually dead accurate. Can't say the same for the bearings though lol. I have since switched to KB 3D. Have not measured those. Printed parts and maybe angle and positioning of heat insert are probably the biggest contributing factors. Regardless of the exact cause simple enough issue to resolve in the next version.

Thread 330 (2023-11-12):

V0.2r1 manual page 104: Filament sensor switch should be wired as Normally Open

Kagee, 2023-11-12:
For the filament sensor the pressed switch is the CONTINUE/RUN condition, while a non-pressed switch is the ERROR/STOP.

For endstops this is reversed. A pressed switch is the ERROR/STOP condition, while a non-pressed switch is the CONTINUE/RUN condition.

A closed loop should be correct condition - filament present (and no brokens wires).
The error condition - filament missing (or broken wire) will be the open loop.
The button is pressed (to the non-normal-position) when there is filament.
Thus one should use Normally Open for the filament sensor.

nemgrea, 2023-12-19:
https://github.com/VoronDesign/Voron-0/pull/337

Closed 2023-12-19.

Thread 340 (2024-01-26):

Guidler prone to slight deformation under higher temperatures, resulting in loss in gripping power

probably-Erwins-Cat, 2024-01-26:
hey guys,
the current guidler is not sufficiently reinforced to keep straight under load and higher temperatures. After deformation, it shows the same failure mode as https://github.com/VoronDesign/Voron-0/issues/308 that you can pull the filament out of the extruder without the groves of the gear properly gripping the filament, i.e., the filament slips through the gear teeth without turning the extruder gears and motor.

I have reproduced my issue a few times, two times involuntarily, one time with my full intention. A rundown:
While printing in a hot environment, i.e., high chamber temp of approx 55°C+, with a heated bed, hotend, and motor, the extruder gear parts, including the guidler, are getting quite warm, warmer than the chamber temp. This can reach the heat deflection temperature (HDT) of some softer ABS/ASA filaments, resulting in a slow creep of the non-reinforced side of the guidler, see images.

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

The first image shows it much clearer than the second. The old and slightly deformed guidler is on the left, a freshly printed on the right.

This causes the gear to misalign. Its rotation axis is no longer parallel to the other gear rotation axis. Higher tensioning cannot resolve this issue (I tried it) as the gear side is fully engaged, but the gripping grove side is moved farther apart. When gently pressing the deformed corner, the extruder immediately works again (as long as you keep pressing)

Similar to the issue https://github.com/VoronDesign/Voron-0/issues/308 I thought it was the too large hole diameter, but it is not. Yes, the reduced play might help a little, but the issue comes back when upper high-temperature and low HDT conditions are met.

Things I tried out and solved the issue:
- take every precaution to reduce temperature towards the guidler, e.g. lowest reasonable chamber temp, hotend and motor current. This, however, limits the printer's capabilities (indirectly). The z-layer adhesion and bed adhesion would suffer.
- switching over to material of higher heat deflection temperature. Unfortunately, many are limited to printing ABS/ASA and many community go-to ABS(+) have shown QC/QA issues and lower HDTs. PC-ABS has high enough HDT but can't really be printed on average-joe printers. My PC-ABS guilder still holds
- modifying the guilder to accept (non-self-tapping) M2x16 as reinforcers. This helps to keep the guilder straighter, i.e. the M2x10 self-tapping screws are too short and do not dig deep enough into the "meat" of the guidler

Things that weren't sufficient:
- lowering the tension to a minimum. The force at the lowest possible tensioning that still pushes the filament reasonably is still too high when the HDT is reached.

Recommendations and things to look into:
- Take a look at the guilder again and check if changing the M2x10 self-tapping screw (that has an effective length of 9mm) can officially be changed to something like M2x16.
- Somehow, make the lower part beefier to resist deflection. This requires a change of other parts to make room for that.
- intentionally add a small tilt of the rotational axis of the gear of the guidler for compensation. Alternatively, the side where the tensioning knob and the latch meet can be slightly wedged, so that the tensioning knob also induces a slight torsion to the guidler for compensation.

fhupfi, 2024-03-01:
Experienced the same issue.

As it is right now, the pink marked portion of the guidler is to weak for the usage in enclosed chambers, when printed from ABS.
- A M2 Bolt is in my eyes not suitable to take the torsional force. Also it doesnt solve the problems root cause.
- i fully support your solution to make the guidler beefier.
- most important: take the torsion (green Arrow) out of the guidler, by bringing the orange marked Forces (pivot point, hobb of the BMG Gear tensioning screw) as close as possible in the dashed red line.

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

NerdyGriffin, 2024-06-19:
This issue is made worse by the fact that the anti-squish screw is even farther from the tensioner spring than the filament path is from the tensioner, so the torsion @fhupfi describes gets worse when using flexible/squishy filament. I attempt to describe this in a comment in another issue https://github.com/VoronDesign/Voron-0/issues/348#issuecomment-2178829877

nemgrea, 2024-12-18:
duplicate of #348. closing this one as more discussion has occured on the other entry

Closed 2024-12-18.

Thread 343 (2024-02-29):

Suggested manual changes

Kagee, 2024-02-29:
This is my summary of comments / suggested fixes to the v0.2r1 manual after having completed a build. Please indicate if you would like me to create individual issues for any of the listed pages/issues. I felt like bomarding the github with 20+ issues was a bit much.

Page 104:
  - "Prepare the switch for the Filament runout sensor by soldering wire to the two indicated terminals. This will setup the switch in a Normally Open state which is preferred for this type of use case. If you have a multimeter you can verify that there only should be connection between the terminals while the button is pressed."
  - Is means the default printer config may need to be changed for the filament detection logic to work the correct way. The default is `switch_pin: gpio16`, i had to change to `switch_pin: !gpio16`

Page 116/118: It is possible to swap the lower parts on right/left by rotating them 90 degrees. Suggest changing the perspective (maybe making the 4. hole extrution on the bottom part more visible) so it is easier to see that it is mounted incorrectly.

Page 119:
- Top image looks like LDO style metal nut bars? Not BOM part?
- If user does not have printed nut adapter, recommend to insert screws and put on nuts before sliding rain onto extrution.

Page 119-120: Do not preload nuts, insert screws into printed part, partly attach nuts, and then slide printed parts on to extrution. Much easier.

Page 137,138: "The flat side of the belt should only contact smooth bearing surfaces", it says nothing about the toothed side. Mention it is allowed to touch both flat and toothed surfaces.

Page 159: Specify that you want the gear w/o grub screw hole.

Page 164: Gear delivered w/o grub screw installed, add stop for that.

Page 174: Make it clear that first screw is on the opposite side to the first image, away from the adjustment screw.

Page: 191-198: Illustrations indicate mains outlet is installed, but that happens first on page 204.

Page 192: Quite hard to see top right screw, maybe hightlight it/all with circles?

Page 194: Mod/kit comment that your kit may have other instructions on how they suggest you lay out the compartment. Maybe one generic one for the whole chapter?

Page 198: Change last sentence to "If you are using the stock LRS-150, you can find the correct hole distances in the datasheet (<URL>)"

Page 199-200: Make it clearer that this is mounted facing to the rear, not down (possible to misunderstand)

Page: 214-216: Illustrate using the slots. It makes the job MUCH easier, but is not that easy to "get" just from text.

Page 222: Mention that most displays have DuPont or other contacts on the rear of the card, do not HAVE to use side connector

Page: 227: Mount ptfe tube to filament foot BEFORE mounting bottom cover

Page 229: Insert screws for door hinges already here

Page 231, 233:
  - Install magnets at start of chapter like heat set inserts. Allowes glue to set.
  - Add visual guide for magnets, N/S poles, show "attraction" between magnets in latches and handle.
Page 231:
  - Insert magnets into handle (or since magnets was installed into handle at start of chapter) use it to position latches correct distance apart.
  - Mention not to install to high to not collide with top-left door bezel.

Page 233: Possible collision between handle and top left bezel if handle played very high up (i.e. to cover v0.1 holes in panel)

Page 239: Move cam lock screw installation to just before attaching top hat to printer to have a flat bottom on the hat for as long as possible.

nemgrea, 2024-06-09:
https://github.com/VoronDesign/Voron-0/pull/354

Closed 2024-06-09.

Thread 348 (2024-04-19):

Guidler upgrade proposal

Matszwe02, 2024-04-19:
I posted an [issue](https://github.com/VoronDesign/Voron-0/issues/308#issue-1788425942) previously, and now I upgraded the suggested idler design even more

- the standard one couldn't hold very flexible TPU even a tiny bit, now it can grab it so I can't get it out with huge force.

My suggestion implements lowering the axis screw's tolerance and widening the gap on the spring tightening section, thus making the minimal gap between gears low enough to squish even very flexible filaments

Also, this design is based on that previous issue, so also the axis screw's hole is at a tiny angle to ensure that the gear won't twist away from the filament, but rather twist that much so it will be parallel to the other gear

[V0.2 Guidler v4.step.zip](https://github.com/VoronDesign/Voron-0/files/15038331/V0.2.Guidler.v4.step.zip)

Matszwe02, 2024-05-08:
# I will add some graphics to show what this change does exactly.

## shape is very similar to the original one - to be honest it can't be distinguishable. It's changed by fractions of mm in the axis and mating surface.

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

# Front view:
To be honest it doesn't look like a significant change from this perspective

## Before:
> 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

## After:
> 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

# Top view:

Here it's visible: 0.2mm vs 0.6mm gap (on the scrren it's 0.2-something, but I didn't count the tiny bit of the axis skew)

- Thus from original 1.4mm filament path, it's now 1mm!
- Counting different print quality from user to user, I can say that this 1.4mm gap can be wider on some printers, being very close to the 1.75mm. I can imagine some tpus easily squish by that 0.3mm.

## Before:
> 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

## After:
> 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

nemgrea, 2024-05-09:
the images and measurements in the "BEFORE" screenshot are not accurate. the cad model is modeled in a symetric constrained state that does not represent the actual position of the gears when there is no filament in the toolhaed.

there is a gap between the guidler and the shuttle on purpose. the thumb screw spring is always trying to close this gap. if we add a hinge mate to this component you can see how the guidler will actually be sitting when the spring is tensioned.

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

you can also see that this state puts the drive gear and idler gear very close to the maximum possible meshing that the gears can do. (in fact most people can feel the "gritty" feel of those gears bottoming out when they spin the 50T without filament present in the assembly)

we can see below that the available space for the filament in the CAD modeled position is 1.6mm

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

however again this is not the minimum position that the gears can reach.

below we can see the same measurement but when the gears are closer to their minimum gap position and we observe that it is much closer to 1.4mm

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

lastly to decrease this 1.4mm dimension further no changes to the guidler are needed, we can simply move the face of the shuttle component back and increase the available travel of the guidler swing arm. however remember that there is a hard limit on the minimum gap that the two BMG gears can achieve due to the gear teeth bottoming out and preventing the two parts from getting any closer to each other.

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

Matszwe02, 2024-05-09:
Thanks for pointing the inaccuracy in my measurements - I used the fusion default model without rotating the guidler to its desired position. However, that doesn't change the fact that my voron couldn't print reliably with the standard design. One of my proposed changes - tilting the guidler axis, helps with the issue of teeth being too close to each other. Maybe that's only my issue, but I experienced a tiny bit of play in the guidler axis, which caused the little backlash that was enough to lose the grip. So maybe my proposed changes will enhance quality on lower quality guidler prints, as it allows for more inaccuracy than the original one.

If my suggested new guidler will be used, there will be close to no difference with the good-quality guidler, as it's affecting the normal working very little, all it does is to allow for more space to squish softer or thinner filaments.

NerdyGriffin, 2024-06-19:
I also support this change because I had similar issues with the mini-SB and I ended up fixing it by adding a shim washer to the mating surface that @Matszwe02 is suggesting to change.

I know there are some issues with the way he presented the measurements, but the real-world results of the suggested change do effectively solve a common issue with the current guilder design.
Due to the fact that the "minimum gap" adjustment screw (referred to as the "ANTI SQUISH THINGYMAJIG" in the manual) is over by the filament path rather than inline with the shuttle and spring, there is a long-term issue where the spring-side gap will creep tighter due to the constant spring pressure and eventually cause the extruders gears to mesh too tightly and bind up. If you adjust the anti-squish screw to increase the gap, it will print fine for a while, but over time the spring pressure will warp the guilder and force the gears closer again. This uneven creep/warping can eventually get so severe that you can have the gear-side gap of the drive gears binding up while the filament-side gap is large enough to slide filament straight through as if it were unlatched (regardless of the anti-squish screw position).

This issue is more common when printing flexible filament because the squishy filament allows all the clamping force to be on the anti-squish screw rather than on the filament itself. The distance between the spring and the anti-squish screw is larger than the distance between the spring and filament path, so the unwanted torque exerted on the guilder is higher (same forces but exerted farther apart = stronger torque around the z-axis to warp the guilder)

**TLDR**:The real issue is not the size of the filament or gear gap as seen in the CAD. Rather, the issue is the fact that this gap changes over time due to the uneven pressure from the tensioner spring and the anti-squish screw.

This is not an issue on the full size StealthBurner because the anti-squish screw in inline with the guilder shutter and spring, so the spring does not exert any unintended twisting force on the guilder.

What the suggested change from @Matszwe02 effectively does is adjust the physical limit of how closely the gear side of the guilder can mesh when the latch is latched, so that the gears cannot get too close and bind up. In other words, it is compensating for the lack of an anti-squish screw on the gear-tooth side of the guilder.

Ideally, the solution would be to move the anti-squish screw forward so that it is directly underneath the shuttle (like in the full size StealthBurner), but that may be difficult or impractical in miniSB due to the size constraints.

Matszwe02, 2024-06-25:
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

Thanks for your observations. If I understand you correctly, you mention mostly the deformation of that part due to these pretty big forces from the constant tension applied to the filament. As it's really a thing (I had to print it with twice the perimeters and 100% infill to make sure it's as solid as possible), my post mostly mentions the lack of the grab "out of the box", as freshly printed guidler cannot print tpu. (so my change extends the possible creep that won't yet cause extrusion issues) Also I saw it's rubbing on the thread of a bolt that's it's axle, so I think this part is just flawed in many ways.

dr-occams-r, 2024-09-13:
I can confirm both this problem (limited grip) and the deformation problem #340.  I just assumed it was my build or prints the problem since the Voron V0 should just work robustly for printing TPU and also for printing ABS (higher temps)

Here are several notes that might help other users and/or the project:

-I observed part deformation at regular print temperatures, see #340 possible solution is reducing amps of extruder motor as it is probably adding heat to the part.

-The "anti-squish screw" is documented as required, but I don't seen how the tension could be so high to cause failure of the printing.  However, if the "anti-squish screw" is being pressed against, the part will deform, as mentioned in #340.  So what is the point of it?  Maybe mark is as optional or remove it?  In my case, it only caused problems and no benefit.  Tension should be controlled by the knob and users should be familiar with this.

-I manually sanded the part down (basically the same as the suggested upgraded part), once it worked, I figured others have have had the same problem and found these discussions.  The part definitely needs to be updated to be tighter on the filament, if desired, and also tolerant to slight variations that come with printing the parts.
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

-The part should definitely be printed at 100%, as others have mentioned.

@Matszwe02:
-Is this the same part? Will you be keeping it updated with any further changes you make?
https://www.printables.com/model/848709-voron-v0-0-02-v02-improved-guidler

-Is there any way to make the part beefier as suggested in issue #340?

-Do you see any problems with making the hole deeper for an M2x16 as suggested in #340?

I will do my next builds / rebuilds with the suggested part and report back.

Matszwe02, 2024-09-13:
@dr-occams-r  thanks for the reply

Yes, that's the same part

I basically think the whole design is flawed, as this axis is constantly experiencing a twisting force.

For now I don't have any plans to modify it, I didn't experience any heat creep so I don't know which part of it needs to be beefier. You can download the step file from printables and post a remix, or suggest the modification.

I also suggest to print everything 100% solid, with as many perimeters as reasonable (I think I had 5 or higher)

disney7, 2024-12-02:
I just wanted to jump in and say that I have this same issue with flexible filaments. My V02 with the Mini StealthBurner grips regular filament superbly, but I can pull TPU out very easily by hand and the extruder won't feed it reliably at all. No issues with my old V01 that has the pre-StealthBurner setup. I'm going to print and try Matszwe02's modified part and will report back.

Driftrotor, 2025-05-14:
now this is interesting, i had similar issues but traced mine back to the pivot screw in the guidler.
over time the hole would ware and become larger until the filament could not be moved consistently due to the guidler being able to twist off axis.
knowing that my personal issue was with the screw being the pivot and that the threads were causing the ware on the printed part i opted to swap it out for a 3mm pin.
i modified the guidler, extruder plate and front cowing for accept the 3mm pin and this for me solved my issue and had been working for me for over a year now with no signs of ware on the parts.
i'm not 100% against the idea that heat soak and pressure are factors involved here but i printed my modified parts with Voron print settings and am yet to see issues arising from these factors.
i personally recommend that a shoulder bolt be used instead of regular type screws for this particular part (guidler pivot) as the cost will be low and also readily available.

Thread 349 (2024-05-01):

Kyleisah RUINED the V0.2 CAD!!!!!!!

kyleisah, 2024-05-01:
I noticed I have some of the panels misaligned, so I gotta fix it. This issue is here to hold me accountable.

Items to fix:
- panel placement.
- clip placement.
- linear rail placement for Y axis might not be correct, will need to confirm because it might depend on order of assembly. (1mm gap between YMAX and rear of gantry, which might be intentional).
- tophat placement.
- hardware is not instanced, there are several copies.
- bodies are not aligned to the origin to export to the slicer correctly facing the buildplate.
- leadscrew is not correctly modeled (dovetail threads rather than trapezoidal).
- miniSB components not evenly spaced.
- raspberry Pi and SKR Pico should be simplified (render models left in).
- switch to the typical heat-set insert models we use.

Items to consider:
- rather than providing multiple STEP/F3D files for every hotend mount, toolhead, ADXL mount, etc, we have one STEP file and one F3D containing everything related to CAD. F3D is not a requirement here, but I like providing it because the materials/appearances look nice, and joints to open and close the door and tophat are fun.
- DIN Rail option should be shown, since it's supported, barring any HATs or PCBs on Raspberry Pi.
- Z chain is a little wonky and should probably be fixed,
- provide single-body side skirt STLs for those who wish to use them
- modeled reverse bowden tube and filament need help (never really liked how they turned out, will probably just leave it alone to maintain continuity with the manual).
- Model a faux umbilical cable.
- any changes to printed files desired should be lumped into the eventual PR that will close this issue, pending approval from the lead dev, Nemgrea.

Things that will not change:
- kyleisah being sowwy

nemgrea, 2024-08-22:
bump

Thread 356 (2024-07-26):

Intruction manual P.109 Voron 0.2r1 2024-05-07 Bad screw lenght

Carlsans, 2024-07-26:
On the Z motor mount, the lower diagram, I really needed M3x10, not M3x8. Since they are hard to install, it would be good to have it right from the start.

Carlsans, 2024-07-27:
I realized that was one one the nuts I did not use a no drop nut because I did not have printed any at the time. The manual say that no drop nut are not supported by voron but yet they are expected. The solution would be either to use the correct length for user who don't use no drop nut or to officially include the use of no drop nut in the manual. The second solution would be very nice since it would allow the user to select the correct no drop nut size in advance. I had to heat gun the idler no drop nut because they were to long. Thanks for your good work :)

Carlsans, 2024-07-28:
Had another issue with bare preloaded nuts. Had to add 2mm to nut length.

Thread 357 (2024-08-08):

Require tach fan on all new kits

Carlsans, 2024-08-08:
I don't know if you have any power there but it need to be said. I bought a kit from a company I wont disclose here. I went with a dragon hotend. Has you may know, kit fans are reputed to be the cheapest. After less than a week, my hotend fan failed. The hotend mount melted and the hotend forced by pression from the extruder crashed in the bed. The main issue there is that the mount will melt if the fan fail. For me that's a more than major issue, I left my printer for 30 minutes and here is the result :
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
That's how bad the bed was scratched. The kirigami bed absorbed most of the shock even bending it.
With the way kit sellers are concerned with the fan problem (they are not). I think the best way to make all voron printers safe in that regard would be to propose kits that enforce the use of tach fans. Even the best fan can and will fail at some time.

nemgrea, 2024-08-08:
we cannot force kit sellers to use specific parts, we can look at changing the official sourcing guide to include a tach fan but beyond that we have no power in the curation of 3rd party printer kits.

just to be clear this was a standard dragon hoted NOT a dragon HF hotend correct?

Carlsans, 2024-08-08:
Yes it is the standard flow. The hotend screws just went right throught the abs part.
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
the other way to fix this would be to have a mount that is completly made of metal so it won't melt.

Carlsans, 2024-08-08:
maybe the use of oversized washers would have delayed the failure...

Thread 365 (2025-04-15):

Cam Lock/Extrusion Tophat Screw Offset Inconsistency

SnoWFLakE0s, 2025-04-15:
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

Self explanatory issue. As of the current CAD model, the screw in the extrusion tophat that mates with the cam lock screw is not actually at the 5mm offset as specified in the manual.

hartk1213, 2025-04-15:
There is nothing wrong with that,

If you read the manual and look at the diagram it's measuring from the head of the screw , the head of an m3 BHCS is 1.65mm so the exposed thread of 3.35mm plus the 1.65mm is the 5mm mentioned in the manual

SnoWFLakE0s, 2025-04-15:
> There is nothing wrong with that,
>
> If you read the manual and look at the diagram it's measuring from the head of the screw , the head of an m3 BHCS is 1.65mm so the exposed thread of 3.35mm plus the 1.65mm is the 5mm mentioned in the manual

My mistake, bad issue. Disoriented by the lock actually colliding w/ the screw. Will close

SnoWFLakE0s, 2025-04-15:
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

I understand--I know firsthand what a decentralized engineering process turns out like. I've been trying to optimize motion parts for subtractive manufacturing, and as a result I'm heavily scrutinizing the model. Great work, thank you.

Closed 2025-04-15.

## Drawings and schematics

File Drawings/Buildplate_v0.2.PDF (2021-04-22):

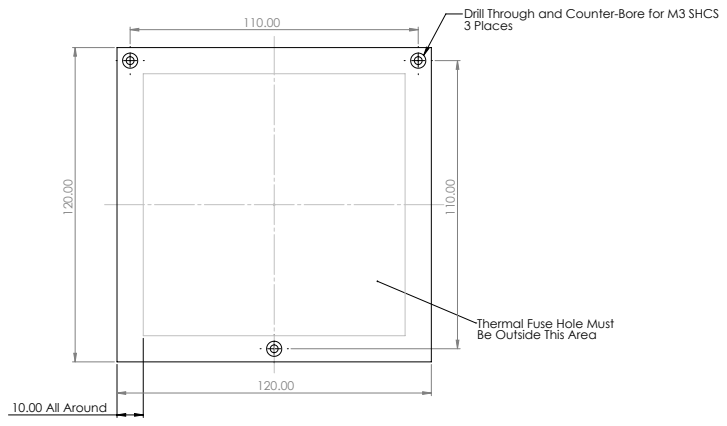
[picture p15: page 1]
10.00 All Around

Drill Through and Counter-Bore for M3 SHCS
3 Places

Thermal Fuse Hole Must
Be Outside This Area

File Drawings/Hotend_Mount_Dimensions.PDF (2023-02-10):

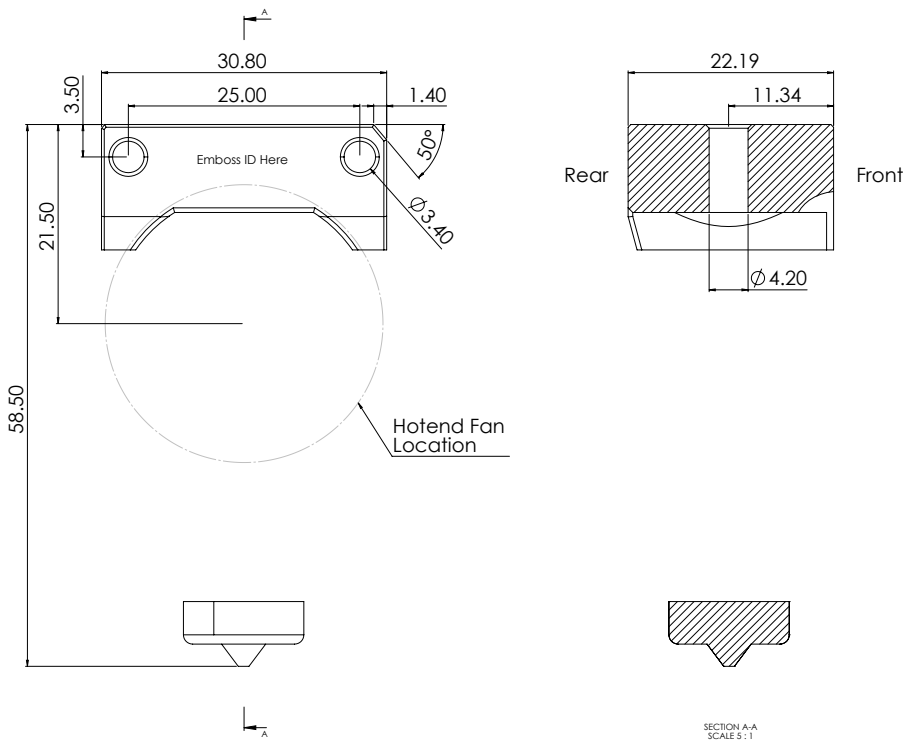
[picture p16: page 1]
Hotend Fan; SECTION A-A SCALE 5 : 1

Emboss ID Here

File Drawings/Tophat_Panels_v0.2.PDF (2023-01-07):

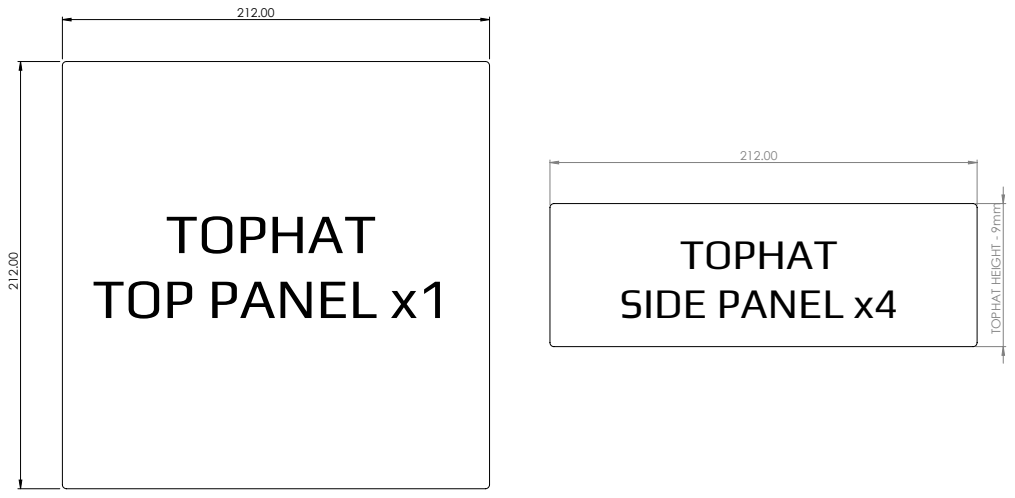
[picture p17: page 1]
TOPHAT HEIGHT - 9mm; TOP PANEL x1; SIDE PANEL x4

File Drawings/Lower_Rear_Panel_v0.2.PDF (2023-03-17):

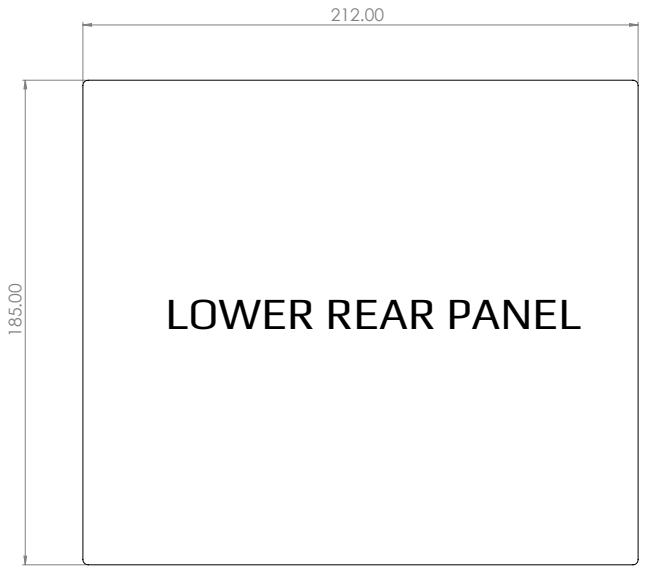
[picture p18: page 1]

LOWER REAR PANEL

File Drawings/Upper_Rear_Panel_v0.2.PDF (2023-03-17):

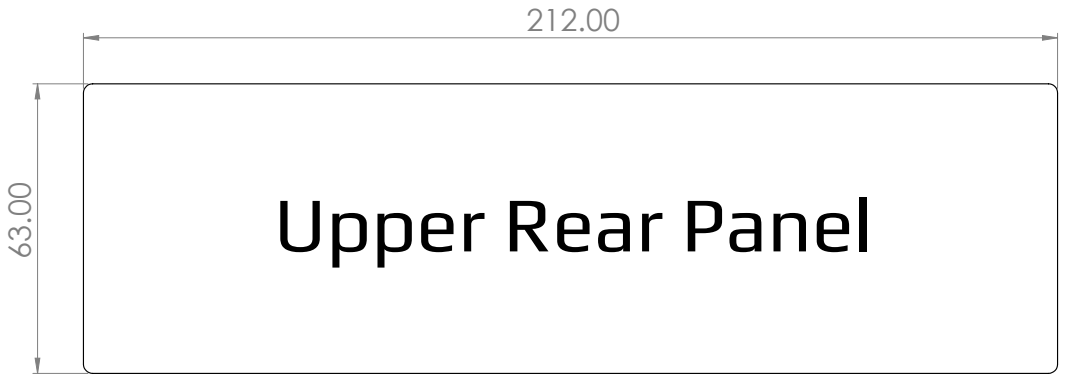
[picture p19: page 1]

Upper Rear Panel

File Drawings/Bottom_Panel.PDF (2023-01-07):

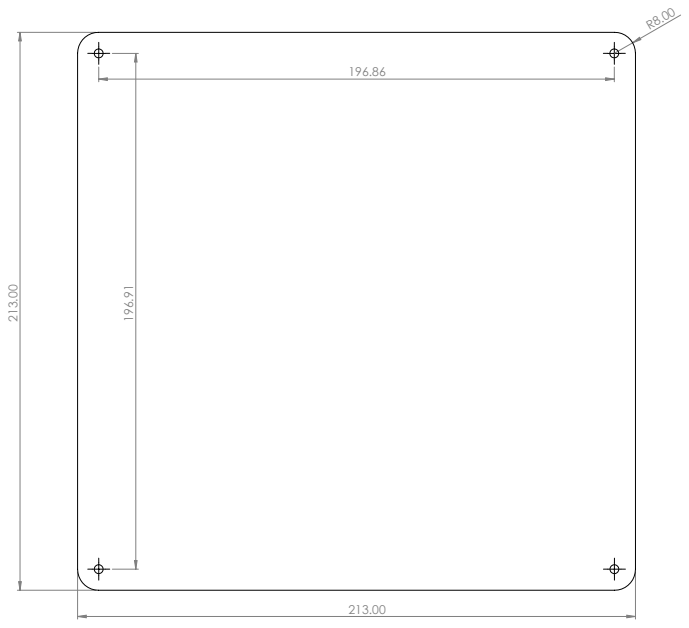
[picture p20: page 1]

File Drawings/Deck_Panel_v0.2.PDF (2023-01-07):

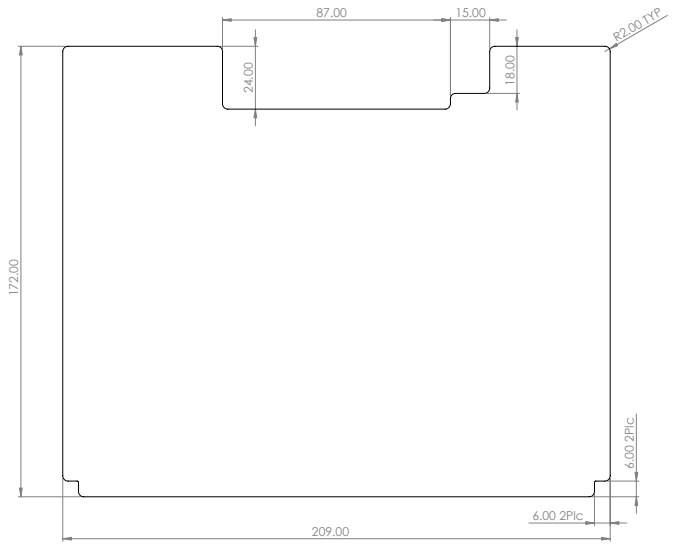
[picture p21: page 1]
6.00 2Plc; 6.00 2Plc R2.00 TYP

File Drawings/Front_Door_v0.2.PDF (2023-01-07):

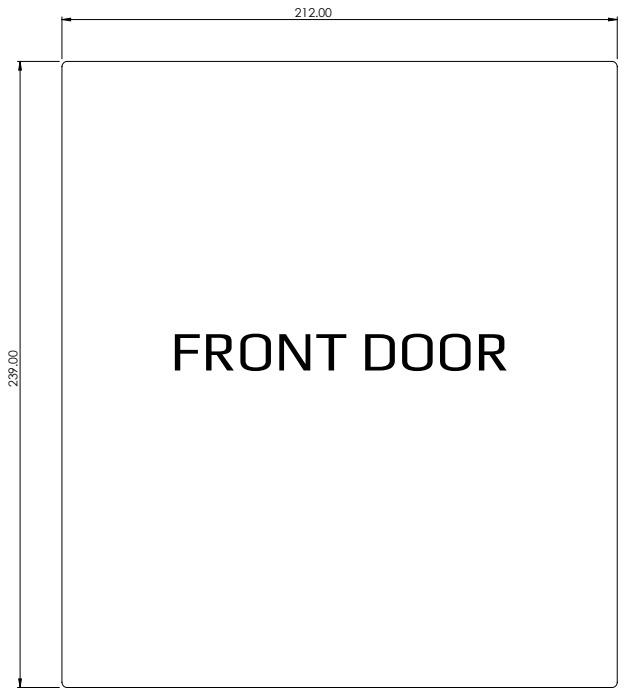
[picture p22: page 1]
FRONT DOOR

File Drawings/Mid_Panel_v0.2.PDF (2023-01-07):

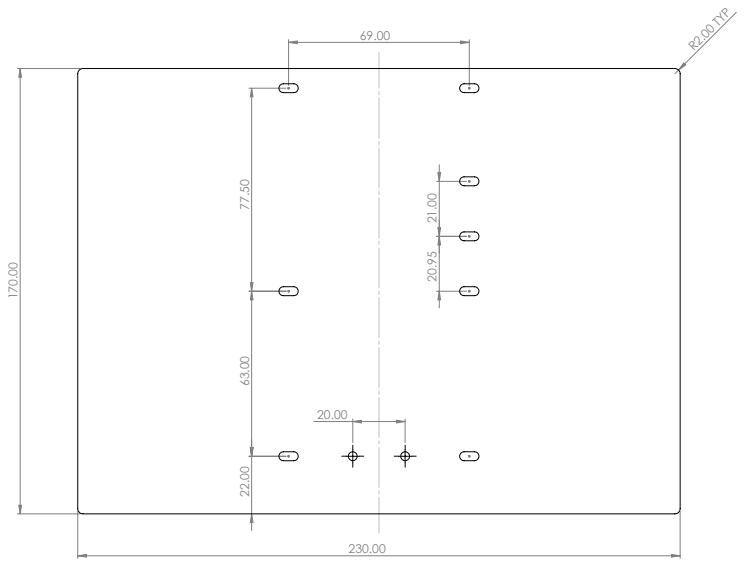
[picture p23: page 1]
R2.00 TYP

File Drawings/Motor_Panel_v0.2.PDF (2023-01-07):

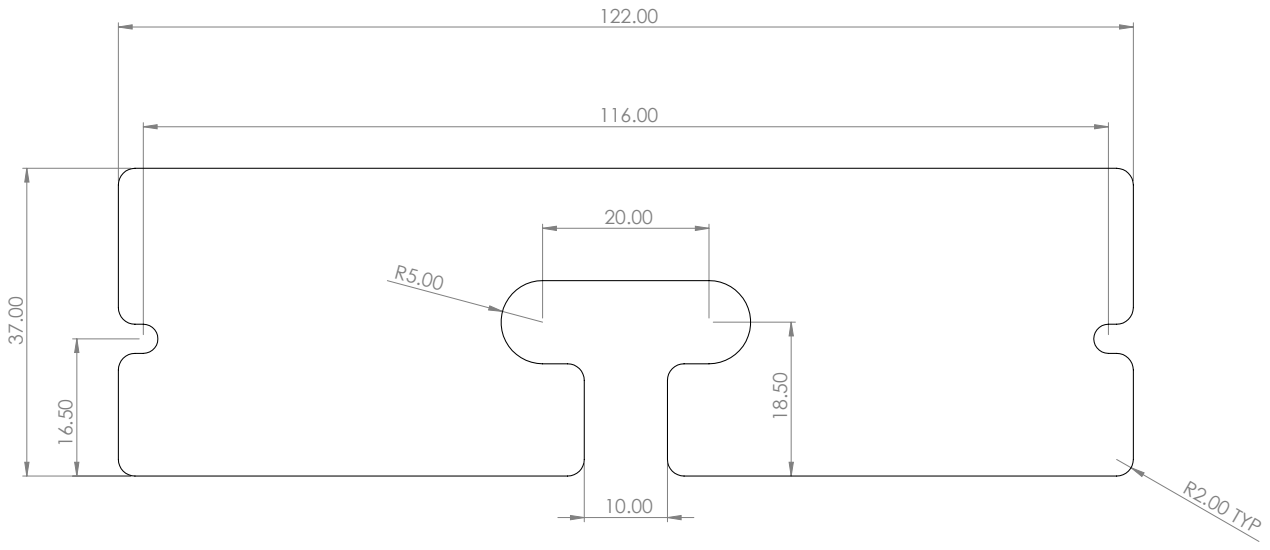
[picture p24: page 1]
R2.00 TYP

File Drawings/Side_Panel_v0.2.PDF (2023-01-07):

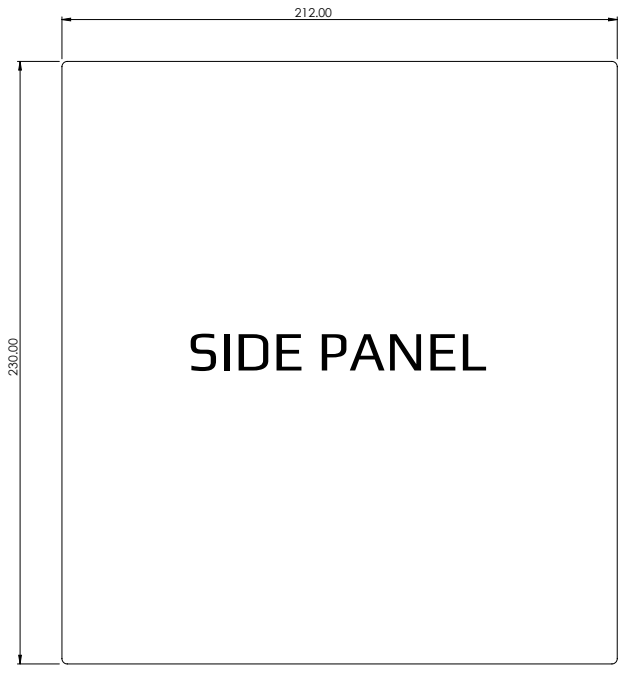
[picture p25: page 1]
SIDE PANEL

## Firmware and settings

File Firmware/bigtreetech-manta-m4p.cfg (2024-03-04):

[include mainsail.cfg]
# This file contains common pin mappings for the BIGTREETECH Manta M4P
# To use this config, the firmware should be compiled for the
# STM32G0B1 with a "8KiB bootloader" and USB communication.

## Voron Design VORON 0.2 SKR Mini E3 V3 config

## *** THINGS TO CHANGE/CHECK: ***
## MCU path                                                                     [mcu] section
## Z and Extruder motor currents                                                [tmc2209 stepper_*] sections. Uncomment the stepper motor you have
## Full steps per rotation for Extruder                                         [extruder] section
## Thermistor types                                                             [extruder] and [heater_bed] sections - See https://www.klipper3d.org/Config_Reference.html#common-thermistors for common thermistor types
## Motor currents                                                               [extruder] [stepper] and [_HOME_X/Y] macro sections
## PID tune                                                                     [extruder] and [heater_bed] sections
## Fine tune E steps                                                            [extruder] section
## For more info                                                                check https://docs.vorondesign.com/build/startup/#v0

[mcu]
#####################################################################
# Obtain definition by "ls -l /dev/serial/by-id/"
#####################################################################
serial: /dev/serial/by-id/usb-Klipper_stm32g0b1xx_REPLACE_WITH_YOUR_VALUE

[temperature_sensor mcu_temp]
sensor_type: temperature_mcu
min_temp: 0
max_temp: 100

[temperature_sensor host_temp]
sensor_type: temperature_host
min_temp: 10
max_temp: 100

[printer]
kinematics: corexy
max_velocity: 200
max_accel: 2000
max_z_velocity: 15
max_z_accel: 300
square_corner_velocity: 6.0

#####################################################################
#      X/Y Stepper Settings
#####################################################################

[stepper_x]
step_pin: PC6
## Refer to https://docs.vorondesign.com/build/startup/#v0
dir_pin: PA14                                                       # Check motor direction in link above. If inverted, add a ! before PB12
enable_pin: !PC7
rotation_distance: 40
microsteps: 32
full_steps_per_rotation: 200                                        # Set to 400 for 0.9° degree stepper motor, 200 is for 1.8° stepper motors
endstop_pin: tmc2209_stepper_x:virtual_endstop                      # Using Virtual Endstop or sensorless homing, make sure you install the jumper on the controller under the stepper
position_endstop: 120
position_max: 120
homing_speed: 20                                                    # for sensorless homing it is recommended not to go above 40mm/s  
homing_retract_dist: 0

[tmc2209 stepper_x]
uart_pin: PB12
interpolate: False
# run_current: 0.0            
# you need to calculate the run_current value using the equation (rated_motor_current * 0.707 = Maximum_run_current) start with a value that is about 60%-70% of your maximum value.sense_resistor: 0.110
stealthchop_threshold: 0                                            # Set to 999999 to turn stealthchop on, and 0 to use spreadcycle
diag_pin: ^PC0                                                      # YOU NEED TO JUMP THIS DIAG PIN ON YOUR BOARD FOR SENSORLESS HOMING TO WORK
driver_SGTHRS: 255                                                  # this is set to 255 which is the MAX sensitivity for sensorless homing, you will need to tune this later

[stepper_y]
step_pin: PB10
## Refer to https://docs.vorondesign.com/build/startup/#v0
dir_pin: PB2                                                        # Check motor direction in link above. If inverted, add a ! before PB2
enable_pin: !PB11
rotation_distance: 40
microsteps: 32
full_steps_per_rotation: 200                                        # Set to 400 for 0.9° degree stepper motor, 200 is for 1.8° stepper motors
endstop_pin: tmc2209_stepper_y:virtual_endstop  
position_endstop: 120
position_max: 120
homing_speed: 20                                                    # for sensorless homing it is recommended not to go above 40mm/s  
homing_retract_dist: 0

[tmc2209 stepper_y]
uart_pin: PC10
interpolate: False
# run_current: 0.0            
# you need to calculate the run_current value using the equation (rated_motor_current * 0.707 = Maximum_run_current) start with a value that is about 60%-70% of your maximum value.sense_resistor: 0.110
stealthchop_threshold: 0                                            # Set to 999999 to turn stealthchop on, and 0 to use spreadcycle
diag_pin: ^PC1                                                      # YOU NEED TO JUMP THIS DIAG PIN ON YOUR BOARD FOR SENSORLESS HOMING TO WORK
driver_SGTHRS: 255                                                  # this is set to 255 which is the MAX sensitivity for sensorless homing, you will need to tune this later

#####################################################################
#   Z Stepper Settings
#####################################################################

[stepper_z]
step_pin: PB0
dir_pin: !PC5                                                       # Remove the ! before PC5 if motor direction is inverted.
enable_pin: !PB1
rotation_distance: 8                                                # For T8x8 integrated lead screw
microsteps: 32
endstop_pin: ^PC2
position_endstop: 120
position_max: 120
position_min: -1.5
homing_speed: 20
second_homing_speed: 3.0
homing_retract_dist: 3.0

[tmc2209 stepper_z]
uart_pin: PC9
interpolate: False
## For OMC (StepperOnline) 17LS13-0404E-200G 0.4A 
#run_current: 0.2
## For LDO-42STH25-1004CL200E 1.0A
#run_current: 0.37
sense_resistor: 0.110
stealthchop_threshold: 0                                            # Set to 999999 to turn stealthchop on, and 0 to use spreadcycle
# if your Z motor is noise try setting this value to 9999

#####################################################################
#   Extruder
#####################################################################

[extruder]
step_pin: PB3
dir_pin: PB4                                                        # Add ! if moving opposite direction
enable_pin: !PD5
#full_steps_per_rotation: 200                                       # Set to 200 for LDO 1.8° stepper motor, and set to 400 for OMC(StepperOnline) 0.9° stepper motor
rotation_distance: 22.23                                            # See calibrating rotation_distance on extruders doc
gear_ratio: 50:10                                                   # For Mini Afterburner
microsteps: 32
nozzle_diameter: 0.400
filament_diameter: 1.750
heater_pin: PC8
## Check what thermistor type you have. See https://www.klipper3d.org/Config_Reference.html#common-thermistors for common thermistor types.
## Use "Generic 3950" for NTC 100k 3950 thermistors
#sensor_type:
sensor_pin: PA0
control: pid                                                        # Do PID calibration after initial checks
pid_Kp: 28.182
pid_Ki: 1.978
pid_Kd: 100.397
min_temp: 0
max_temp: 270
min_extrude_temp: 170
max_extrude_only_distance: 150
max_extrude_cross_section: 0.8
pressure_advance: 0.0                                               # See tuning pressure advance doc
pressure_advance_smooth_time: 0.040

[tmc2209 extruder]
uart_pin: PA13
interpolate: False
## For OMC (StepperOnline) 14HR07-1004VRN 1A 0.9°
#run_current: 0.5   # for OMC 14HR07-1004VRN rated at 1A
## For LDO LDO 36STH17-1004AHG 1A 1.8° 
#run_current: 0.3   # for LDO 36STH17-1004AHG
## For LDO LDO 36STH20-1004AHG 1A 1.8° 
#run_current: 0.6   # for LDO 36STH20-1004AHG
sense_resistor: 0.110
stealthchop_threshold: 0                                            # Set to 0 for spreadcycle, avoid using stealthchop on extruder

#####################################################################
#   Bed Heater
#####################################################################

[heater_bed]
heater_pin: PD8
## Check what thermistor type you have. See https://www.klipper3d.org/Config_Reference.html#common-thermistors for common thermistor types.
## Use "Generic 3950" for Keenovo heaters
#sensor_type:
sensor_pin: PC4
smooth_time: 3.0
#max_power: 0.6                                                     # Only needed for 100w pads
min_temp: 0
max_temp: 120
control: pid                                                        # Do PID calibration after initial checks
pid_kp: 68.453
pid_ki: 2.749
pid_kd: 426.122

#####################################################################
#   Fan Control
#####################################################################

[heater_fan hotend_fan]
# FAN1
pin: PD3
max_power: 1.0
kick_start_time: 0.5
heater: extruder
heater_temp: 50.0
#fan_speed: 1.0                                                     # You can't PWM the delta fan unless using blue wire
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

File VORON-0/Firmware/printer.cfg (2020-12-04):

# This file contains common pin mappings for the BIGTREETECH SKR
# MINI. To use this config, the firmware should be compiled for the
# STM32F103 with a "28KiB bootloader".

# The "make flash" command does not work on the SKR mini. Instead,
# after running "make", copy the generated "out/klipper.bin" file to a
# file named "firmware.bin" on an SD card and then restart the SKR
# mini with that SD card.

# See the example.cfg file for a description of available parameters.

[mcu]
serial: /dev/serial/by-id/usb-Klipper_stm32f103xe_37FFD8054246383440750857-if00

[stepper_x]
step_pin: PB13
dir_pin: PB12
enable_pin: !PB14
step_distance: .0125
endstop_pin: PC0 
position_endstop: 120
position_max: 120
homing_speed: 20   #Max 100
homing_retract_dist: 5
homing_positive_dir: true

[tmc2209 stepper_x]
uart_pin: PB15
microsteps: 16
interpolate: True
run_current: .25
hold_current: .25
sense_resistor: 0.110
stealthchop_threshold: 500

[stepper_y]
step_pin: PB10
dir_pin: PB2
enable_pin: !PB11
step_distance: .0125
endstop_pin: PC1
position_endstop: 120
position_max: 120
homing_speed: 20   #Max 100
homing_retract_dist: 5
homing_positive_dir: true

[tmc2209 stepper_y]
uart_pin: PC6
microsteps: 16
interpolate: True
run_current: .25
hold_current: .25
sense_resistor: 0.110
stealthchop_threshold: 500

[stepper_z]
step_pin: PB0
dir_pin: PC5
enable_pin: !PB1
step_distance: .0025 #for T8x8 lead screw
#step_distance: .000625 #for T8x2 lead screw
endstop_pin: PC2
#position_endstop: -.10
position_max: 120
position_min: -1
homing_speed: 10   #Max 100
second_homing_speed: 3.0
homing_retract_dist: 3.0

[tmc2209 stepper_z]
uart_pin: PC10
microsteps: 16
interpolate: True
run_current: .25
hold_current: 0.25
sense_resistor: 0.110
stealthchop_threshold: 500


[extruder]
step_pin: PB3
dir_pin: PB4
enable_pin: !PD2
step_distance: .0024 #calibrate this value for your individual printer!!
nozzle_diameter: 0.400
filament_diameter: 1.750
heater_pin: PC8
sensor_type: EPCOS 100K B57560G104F
sensor_pin: PA0
control: pid
pid_Kp: 22.2
pid_Ki: 1.08
pid_Kd: 114
min_temp: 0
max_temp: 270
min_extrude_temp: 170
max_extrude_only_distance: 780.0
max_extrude_cross_section: .8
Pressure_advance: 0.0
pressure_advance_smooth_time: 0.040

[tmc2209 extruder]
uart_pin: PC11
microsteps: 16
interpolate: True
run_current: 0.2
hold_current: 0.2
sense_resistor: 0.110
stealthchop_threshold: 500

[heater_bed]
heater_pin: PC12
sensor_type: NTC 100K beta 3950
#sensor_type: NTC 100K MGB18-104F39050L32
sensor_pin: PC3
smooth_time: 3.0
max_power: 0.6
control: pid
min_temp: 0
max_temp: 120
pid_kp: 58.437
pid_ki: 2.347
pid_kd: 363.769

[printer]
kinematics: corexy
max_velocity: 250
max_accel: 2000
max_z_velocity: 10
max_z_accel: 30
square_corner_velocity: 5.0

[heater_fan hotend_fan]
# Hotend Fan
pin: PA8
max_power: 1.0
kick_start_time: 0.5
heater: extruder
heater_temp: 50.0
#If you are experiencing back flow, you can reduce fan_speed
#fan_speed: 1.0

[fan]
# Print Cooling Fan - XYE board, Fan Pin
pin: PC9
kick_start_time: 0.5
#depending on your fan, you may need to increase or reduce this value
#if your fan will not start
off_below: 0.13
cycle_time: 0.010

[idle_timeout]
timeout: 1800


[homing_override]
axes: z
set_position_z: 0
gcode:
   G90
   G0 Z5 F600
   G28 X Y
   G0 X30 Y0 F3600 
   
   G28 Z
   G0 Z10 F1800
   G0 X60 Y60 Z20 F3600

   # Tool to help adjust bed leveling screws. One may define a
# [bed_screws] config section to enable a BED_SCREWS_ADJUST g-code
# command.
[bed_screws]
screw1: 60,5
screw1_name: front screw
screw2: 5,115
screw2_name: back left
screw3: 115,115
screw3_name: back right

[gcode_macro PRINT_START]
#   Use PRINT_START for the slicer starting script - please customise for your slicer of choice
gcode:
    G28                            ; home all axes
    G1 Z20 F3000                   ; move nozzle away from bed
   
[gcode_macro PRINT_END]
#   Use PRINT_END for the slicer ending script - please customise for your slicer of choice
gcode:

    M400                           ; wait for buffer to clear
    G92 E0                         ; zero the extruder
    G1 E-4.0 F3600                 ; retract filament
    G91                            ; relative positioning

    #   Get Boundaries
    {% set max_x = printer.configfile.config["stepper_x"]["position_max"]|float %}
    {% set max_y = printer.configfile.config["stepper_y"]["position_max"]|float %}
    {% set max_z = printer.configfile.config["stepper_z"]["position_max"]|float %}

    #   Check end position to determine safe direction to move
    {% if printer.toolhead.position.x < (max_x - 20) %}
        {% set x_safe = 20.0 %}
    {% else %}
        {% set x_safe = -20.0 %}
    {% endif %}

    {% if printer.toolhead.position.y < (max_y - 20) %}
        {% set y_safe = 20.0 %}
    {% else %}
        {% set y_safe = -20.0 %}
    {% endif %}

    {% if printer.toolhead.position.z < (max_z - 2) %}
        {% set z_safe = 2.0 %}
    {% else %}
        {% set z_safe = max_z - printer.toolhead.position.z %}
    {% endif %}

    G0 Z{z_safe} F3600    ; move nozzle up
    G0 X{x_safe} Y{y_safe} F20000    ; move nozzle to remove stringing
    TURN_OFF_HEATERS
    M107                           ; turn off fan
    G90                            ; absolute positioning
    G0 X60 Y{max_y} F3600          ; park nozzle at rear
	
[gcode_macro LOAD_FILAMENT]
gcode:
   M83                            ; set extruder to relative
   G1 E280 F1800                  ; quickly load filament to down bowden
   G1 E30 F300                    ; slower extrusion for hotend path
   G1 E15 F150                    ; prime nozzle with filament
   M82                            ; set extruder to absolute
    
[gcode_macro UNLOAD_FILAMENT]
gcode:
   M83                            ; set extruder to relative
   G1 E10 F300                    ; extrude a little to soften tip
   G1 E-380 F1800                 ; retract filament completely
   M82                            ; set extruder to absolute

# Sensor Types
#   "EPCOS 100K B57560G104F"
#   "ATC Semitec 104GT-2"
#   "NTC 100K beta 3950"
#   "Honeywell 100K 135-104LAG-J01"
#   "NTC 100K MGB18-104F39050L32" (Keenovo Heater Pad)
#   "AD595"
#   "PT100 INA826"

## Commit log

2020-04-06 V0 STL's (#1)
    * Create README
    * Add files via upload
    * Create V0.0_RC1
    * Delete V0.0_RC1
    * Create README
    * Add files via upload
    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
    [2mm_Bottom_Corner_Front_x1.STL, 2mm_Bottom_Corner_Rear_mirror_x1.STL, 2mm_Bottom_Corner_Rear_x1.STL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]
2020-04-06 Minor clean-up (#2)
    Remove apostrophes from directory names and add travis CI script
    [2mm_Bottom_Corner_Front_x1.STL, 2mm_Bottom_Corner_Rear_mirror_x1.STL, 2mm_Bottom_Corner_Rear_x1.STL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]
2020-04-07 Add Pocketwatch STL's (#3)
    * Delete Motor_Frame_x1.STL
    * Delete Pocketwatch_Guts_x1.STL
    * Delete README
    * Delete [a]_Guidler_Door_x1.STL
    * Delete [a]_Latch_Shuttle_x1.STL
    * Delete [a]_Latch_x1.STL
    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
    [2mm_Bottom_Corner_Front_x1.STL, 2mm_Bottom_Corner_Rear_mirror_x1.STL, 2mm_Bottom_Corner_Rear_x1.STL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]
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2020-04-09 new guts version for heatset inserts (#5)
    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
    [Pocketwatch_Guts_x1.STL]
2020-04-09 fix issue#6 (#7)
    * Delete V0_Extrusion_Drilling_Guide_x1.STL
    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
    [V0_Extrusion_Drilling_Guide_x1.STL]
2020-04-15 fix stl issues with bed position (#8)
    [T8_Nut_Block_x1.STL]
2020-05-02 pocketwatch alignment fix (#12)
    * Delete VORON_Pocketwatch.STEP
    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
    [Motor_Frame_x1.STL, Pocketwatch_Guts_x1.STL]
2020-05-05 mismatch in mosquito toolhead fixed (#13)
    * Delete Toolhead_Left_Mosquito_x1.STL
    * Delete Toolhead_Right_Mosquito_x1.STL
    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
    [[a]_Latch_x1.STL]
2020-05-11 CAD Assembly/Final Manual (#14)
    * Delete [a]_Belt_Retention_Block_x1.STL
    * Big push
    CAD added
    Manual added
    setup guide added
    * Delete V0_Assembly_Manual.pdf
    * fix pswd
    * stop timmits damn bitching
    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
    [Bowden retainer.stl, Bowden_retainer.stl, Heat_set_thumb_nut.stl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]
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2020-06-22 fix pinouts in config file (#17)
    [[a]_Z_Endstop_Mount_x1.STL, [a]_Z_Endstop_Mount_x1.stl, printer.cfg]
2020-06-24 inverted bed heater to stop run away heating on startup (#19)
    [printer.cfg]
2020-06-27 slight modification to skirts (#20)
    * Delete Skirt_x3.STL
    * Delete Skirt_mirror_x3.STL
    * slightly moved skirt mounting hole
    makes skirt compatible with voron hardware display
    * Delete Skirt_mirror_x3.STL
    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
    [Skirt_mirror_x3.STL, Skirt_x3.STL]
2020-06-28 fix for issue #23 (#24)
    * Delete [a]_Z_Endstop_Mount_x1.stl
    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
    [[a]_Z_Endstop_Mount_x1.STL, [a]_Z_Endstop_Mount_x1.stl]
2020-06-30 Fix reversed facets (#25)
    * Fix reversed facet
    * additional stl repairs
    [2mm_Bottom_Corner_Rear_mirror_x1.STL, 2mm_Bottom_Corner_Side_mirror_x1.STL, 2mm_Top_Corner_Rear_mirror_x1.STL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]
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2020-08-25 Fix Pocketwatch shuttle STL
    [[a]_Latch_Shuttle_x1.STL]
2020-08-25 Fix corrupt rev2 STLs
    [2mm_Bottom_Corner_Rear_mirror_x1.STL, 2mm_Bottom_Corner_Side_mirror_x1.STL, 2mm_TH_Lower_Corner_Clip_Right_x2.stl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]
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2020-09-10 Uncomment required lines from bed heater section (#37)
    In the previous commit, the `SAVE_CONFIG` block was (probably correctly) deleted, which overrode the commented-out heater settings for the heater bed; this breaks the config for people doing a fresh start. This commit uncomments the control section so folks can get started without tripping up on this 🙂
    [printer.cfg]
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2020-10-25 Close holes in blower duct, fixes #38 (#45)
    * Delete [a]_Toolhead_Blower_Duct_Left_TV6_x1.STL
    fix print slicing from issue #38
    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
    [[a]_Toolhead_Blower_Duct_Left_TV6_x1.STL]
2020-11-18 Update printer.cfg and bedScrewMenu.cfg
    Update PRINT_END to keep nozzle within boundaries
    Fix thermistor in heater_bed
    Change heater_bed max power to 0.6
    Fix menu entries of bedScrewMenu.cfg
    [bedScrewMenu.cfg, printer.cfg]
2020-12-03 Changes cycle_time for parts fan
    Changes the cycle_time value for the parts fan to `0.010` which is the default value. The previous value of `0.001` would not work reliably with some fans.
    [printer.cfg]
2020-12-18 Split SKR E3 Mini 1.2 and 2.0 Configs (#53)
    * Adds config options for SKR Mini 2.0
    Adds commented out values to support both SKR Mini 1.2 and 2.0 boards.
    * Makes default dir_pin inverted
    * Split Config Files per Nemgrea's preference
    [bedScrewMenu.cfg, printer.cfg]
2020-12-27 hole tolerance updates (#52)
    * Delete Toolhead_Right_Dragon_x1.STL
    * Delete Toolhead_Left_Dragon_x1.STL
    open m2 holes by 0.3mm
    open m2 holes by 0.3mm
    * Delete Toolhead_Left_Threaded_V6_x1.STL
    * Delete Toolhead_Right_Threaded_V6_x1.STL
    open m2 holes 0.3mm
    bearing hole smaller by 0.15mm
    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
    [Pocketwatch_Guts_x1.STL, Toolhead_Left_Dragon_x1.STL, Toolhead_Left_Threaded_V6_x1.STL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]
2021-01-12 Little easier to print 4-pcs TopHat + Missing 4-pcs TopHat hinge part (#55)
    Added modified STLs
    * Delete TopHat_Left_x2.stl
    Deleted old file 1/2
    * Delete TopHat_Right_x2.STL
    Delete old file 2/2
    Fixed orientation of STLs to be readily printable.
    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
    [TopHat_Left_Hinge_x1.stl, TopHat_Left_x1.stl, TopHat_Left_x2.stl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]
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2021-04-18 Add missed STLs
    [Guidler_DD_x1.stl, Latch_DD_x1.stl, Latch_Shuttle_DD_x1.stl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]
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2021-04-18 Fix borken files
    [A_Drive_Frame_Lower_x1.stl]
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2021-04-18 fix x carriage (#66)
    * Delete X_Carriage_x1.stl
    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
    [X_Carriage_x1.STL, X_Carriage_x1.stl]
2021-04-18 fix file names (#67)
    * Delete XY_Joint_Left_Lower_x1_x1.stl
    * Delete XY_Joint_Left_Upper_x1_x1.stl
    * Delete XY_Joint_Right_Lower_x1_x1.stl
    * Delete XY_Joint_Right_Upper_x1_x1.stl
    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
    [XY_Joint_Left_Lower_x1.stl, XY_Joint_Left_Upper_x1.stl, XY_Joint_Right_Lower_x1.stl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]
2021-04-18 move tools to separate folder (#68)
    * Create README.me
    * Delete T-Nut_Mod_Tool_x1.STL
    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
    [BMG_Shaft_Mod_Spacer_x1.STL, T-Nut_Mod_Tool_x1.STL, V0_Extrusion_Drilling_Guide_x1.STL]
2021-04-18 STL fix (cad error)
    [X_Carriage_90_x1.STL, X_Carriage_x1.STL]
2021-04-19 Fix the fix.
    [X_Carriage_90_x1.STL]
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2021-04-22 Add drawings and DXF's (#74)
    * Create readme.me
    * Create readme.me
    * Create readme.me
    * Create readme.me
    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
    [Deck_Panel_x1.DXF, Front_Rear_v0.1_x2.DXF, Mid_Panel_x1.DXF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]
2021-04-22 Update Assembly_Manual_0.1.pdf (#76)
    page 7 - corrected shim size
    page 11 - tapped ends for f extrusion
    page 35 - changed orientation for clarity
    page 82 - fixed typo
    page 89 - changed to BHCS
    page 92,97,139,140 - corrected hex driver size
    page 125 - fixed typo
    page 146 - changed highlight for clarity
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2021-05-04 part orientation fix (#83)
    * Delete BMG_Shaft_Mod_Spacer_x1.STL
    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
    [BMG_Shaft_Mod_Spacer_x1.STL]
2021-05-05 add missing panel dxf from assembly step-file (#64) (#84)
    * add missing panel dxf from assembly step-file
    Rename existing files with postfix nx indicators for number of copies to laser cut
    create dxf for TopHat_Top, Side_, Door
    modify deck_ to include missing holes
    * change naming convention and removed holes from deck panel
    Change naming convention to match existing parts name_x1 instead of name_1x
    Remove holes from deck panel
    [Back_Panel_V0_x1.DXF, Deck_Panel_Rear_V0_x1.DXF, Deck_Panel_V0_x1.DXF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]
2021-05-05 Revert "add missing panel dxf from assembly step-file (#64) (#84)"
    This reverts commit 02965bb99c45a938ad4bc351baa9c31b6178447e.
    [Back_Panel_V0_x1.DXF, Deck_Panel_Rear_V0_x1.DXF, Deck_Panel_V0_x1.DXF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]
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2021-05-18 add BMO mid body part, restructure toolhead stls for clarity (#91)
    * Delete [a]_Mid_Body_x1.stl
    * Delete X_Carriage_90_x1.STL
    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
    [X_Carriage_90_x1.STL, [a]_Mid_Body_Dragon_x1.stl, [a]_Mid_Body_Mosquito_x1.stl]
2021-05-19 rotate part 180 (#92)
    * Delete [a]_Mid_Body_BMO_x1.STL
    flip part 180
    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
2021-05-26 Example firmware for stock v0.1 build (#93)
    * V0.1 stock firmware
    * Rename readme
    * Tweaks based on feedback
    * More tweaks based on PR feedback
    * Clean
    * More suggested tweaks from @timmit99
    * Comment tweak
    * Tweaked printer.cfg and updated docs
    * Tweak doc
    * Link to docs for AB motors when XY dir wrong, increase max
    [printer.cfg]
2021-06-13 Update Assembly_Manual_0.1.pdf
    closes 99, 100, 101, 104, 106, 108
    Changes:
    page 10/11 - Added H extrusion, C extusion with tapped ends
    page 24 - changed to H extrusion
    page 27 - added threadlocker text
    page 31 - fixed typo
    page 35 - changed to H extrusion
    page 36 - moved z chain link install
    page 38 - removed preloaded nut for z chain
    page 60 - moved z endstop strike bolt
    page 73 - added text to side views
    page 96 - moved z chain link install
    page 99 - added 50mm wire for x end-stop
    page 102 - moved z endstop strike bolt
    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
2021-08-31 Update printer.cfg (#122)
    * Update printer.cfg
    Update for OMC 0.9deg extruder motor
    * Update printer.cfg
    * Update printer.cfg
    Change default extruder run/hold current to LDO motor
    [printer.cfg]
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2021-11-05 Update printer.cfg (#130)
    Update printer.cfg and make it default for LDO kits
    Clean up tabulars
    -Commented motor currents so user has to uncomment the correct one
    -Changed min extrude temp back to 170
    -Reworded and reworked thermistors
    Make X/Y A/B direction clearer
    fix braindead linking
    reword stealthchop/spreadcycle
    Minor description updates
    Consistency
    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
    [printer.cfg]
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2021-12-22 Added new spacers to fix the LDO motor 14mm (#136)
    * Shorter spacer - 14mm to fit LDO motor.
    * Update Strain_Relief_Body_x1.STL
    * Revert "Update Strain_Relief_Body_x1.STL"
    This reverts commit 53292d7554d4518b5c662f12be5ad7029e2c9fc8.
    * Added 1 mm thickness and a taller for better usability
    * Fixed Orientation to be printable as is.
    [Strain_Relief_Body_x1.STL, Strain_Relief_Spacers_LDO_x2.stl]
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2022-01-05 Update sensor types (#133)
    Renamed "NTC 100K beta 3950" to "Generic 3950". This was recently updated in klipper.
    [printer.cfg]
2022-01-06 Revert Strain Relief to original and added warning to printer.cfg for LDO extruder (#142)
    * Add warning to for LDO extruder motor
    A couple of instances of people increasing the current on LDO 36STH17-1004AHG and melting there motor mount or entire toolhead.
    * Revert Strain_Relief_Body_x1 to original
    I thought I reverted this, but it accidentally replaced the original strain relief.
    *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
    [Strain_Relief_Body_x1.STL, printer.cfg]
2022-01-12 support for Revo Voron (#143)
    * Create Readme.md
    * Delete Readme.md
    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
    [[a]_Cowling_Revo_Voron_MULTIBODY_x1.stl, [a]_Cowling_Revo_Voron_x1.stl]
2022-01-12 Fix STLs that fail validation (#144)
    [2mm_Top_Corner_Rear_x1.STL, 2point5mm_Top_Corner_Rear_x1.stl, 3mm_Top_Corner_Rear_mirror_x1.stl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]
2022-01-17 Add skr pico klipper config (#146)
    * rename printer.cfg to skr-mini-v2.0.cfg
    * add klipper config for skr pico v1.0
    * rename skr-mini-v2.0 to skr-mini-E3-v2.0
    [skr-mini-E3-v2.0.cfg, skr-pico-v1.0.cfg]
2022-02-04 config updates, 16>32, interpolate false, remove hold current (#150)
    * Update skr-mini-E3-v2.0.cfg
    * Update skr-pico-v1.0.cfg
    [skr-mini-E3-v2.0.cfg, skr-pico-v1.0.cfg]
2022-02-05 Typo correction
    [skr-pico-v1.0.cfg]
2022-02-15 SKR Mini E3 V3.0 configuration (#149)
    * SKR Mini E3 V3.0 configuration
    Updated configuration to reflect new pin definitions of SKR Mini E3 V3.0.
    * Update skr-mini-E3-v3.0.cfg
    * Update skr-mini-E3-v3.0.cfg
    [skr-mini-E3-v3.0.cfg]
2022-02-19 Correct header of file to match klipper's example config setup instructions (#152)
    [skr-mini-E3-v3.0.cfg]
2022-02-23 Fix skr pico V1.0 config
    move the `[thermistor]` block above of the `[extruder]` block
    [skr-pico-v1.0.cfg]
2022-02-23 Fix skr mini E3 V2.0 config
    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
    [skr-mini-E3-v2.0.cfg]
2022-03-16 revo toolhead fix (#156)
    * Delete [a]_Cowling_Revo_Voron_MULTIBODY_x1.stl
    * Delete [a]_Cowling_Revo_Voron_x1.stl
    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
    [[a]_Cowling_Revo_Voron_MULTIBODY_x1.STL, [a]_Cowling_Revo_Voron_MULTIBODY_x1.stl, [a]_Cowling_Revo_Voron_x1.STL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]
2022-03-16 Enhance E3 mini V3 config (#151)
    - Link to the Klipper thermistor page instead of hardcoding a list that
    might be outdated as comments
    - Add FAN2 config
    [skr-mini-E3-v3.0.cfg]
2022-04-01 Fix file name (No part changes) (#160)
    [[a]_B_Drive_Tensioner_x1.stl]
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2022-04-30 Remove default sensor_types, convert tabs to spaces (#161)
    * Remove default sensor_types
    * Comment out sensor_types, convert tabs to spaces
    * Remove 3950 footnotes, ensure newlines at end of configs
    [skr-mini-E3-v2.0.cfg, skr-mini-E3-v3.0.cfg, skr-pico-v1.0.cfg]
2022-06-27 Update configs for LDO 36STH20-1004AHG (#167)
    * Add run_current for 36STH20-1004AHG, which replaces 36STH17-1004AHG in newer LDO kits.
    [skr-mini-E3-v2.0.cfg, skr-mini-E3-v3.0.cfg, skr-pico-v1.0.cfg]
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2022-12-12 Revo cowling update (#179)
    * Delete [a]_Cowling_Revo_Voron_MULTIBODY_x1.STL
    * Delete [a]_Cowling_Revo_Voron_x1.STL
    * Delete [a]_Cowling_Revo_Voron_MULTIBODY_x1.STL
    * Delete [a]_Cowling_Revo_Voron_x1.STL
    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
    [[a]_Cowling_Revo_Voron_MULTIBODY_x1.STL, [a]_Cowling_Revo_Voron_x1.STL]
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2023-01-08 Voron0.2 (#185)
    * Delete A_Idler_Upper_x1.stl
    * Delete [a]_MiniSB_Cowling_x1.STL
    * Delete [a]_MiniSB_Cowling_Multibody_Logo_x1.STL
    * Delete TH_Lower_Clip_Mirror_x3.stl
    * Delete TH_Lower_Clip_x3.stl
    * Delete TH_Side_Clip_Mirror_x4.stl
    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
    [A_Idler_Upper_x1.stl, TH_Hinge_A_Bottom_x1.STL, TH_Hinge_A_Top_x1.STL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]
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2023-01-08 part orientations updates (#186)
    * Delete TH_Side_Clip_x4.stl
    * Delete TH_Top_Clip_x4.stl
    * Delete TH_Hinge_A_Bottom_x1.STL
    * Delete TH_Hinge_A_Top_x1.STL
    * Delete TH_Hinge_B_Bottom_x1.STL
    * Delete TH_Hinge_B_Top_x1.STL
    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
    [BL_Corner_Bracket.stl, Hinge_A_Top.stl, Hinge_A_bottom.stl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]
2023-01-08 Cowling update (#194)
    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
    [MGN7_Rail_Guide_x2.STL, [a]_MiniSB_Cowling_Multibody_Logo_x1.STL, [a]_MiniSB_Cowling_x1.STL]
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2023-01-08 MiniSB Bowden Fix (#196)
    * Delete [a]_MiniSB_Bowden_ECAS04_x1.stl
    * Delete [a]_MiniSB_Bowden_M10_x1.stl
    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
    [MiniSB_Bowden_Logo_Insert.stl]
2023-01-08 Dxf fix (#197)
    * Delete Bottom_Panel.DXF
    * Delete Deck_Panel_.DXF
    * Delete Front_Door.DXF
    * Delete Mid_Panel.DXF
    * Delete Motor_Panel.DXF
    * Delete Rear_Panel.DXF
    * Delete Side_Panel.DXF
    * Delete Tophat_Top_Panel.DXF
    * Delete Tophat_Side_Panel_80mm.DXF
    * Delete Tophat_Side_Panel_100mm.DXF
    * Delete Tophat_Side_Panel.dxf
    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
    [Bottom_Panel.DXF, Deck_Panel_.DXF, Front_Door.DXF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]
2023-01-08 Stl readme fix (#199)
    * Update Readme.md
    * Update Readme.md
    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
2023-01-16 default sensorless homing cfg updates (#214)
    * default configs update
    updated default cfgs with correct sensorless homing speed values
    added comments about each specific board whether it needs a jumper or not for the diag pin
    updated z homing speed to 20 from 10 since its now going to max
    * Update bigtreetech-skr-3-ez.cfg
    * Update bigtreetech-skr-mini-e3-v2.0.cfg
    [bigtreetech-manta-m4p.cfg, bigtreetech-skr-3-ez.cfg, bigtreetech-skr-mini-e3-v2.0.cfg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]
2023-01-16 Z motor mount rename (#215)
    * renamed Z motor mount to use accent color
    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
    [[a]_Z_Motor_Mount_x1.stl]
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2023-01-19 Update Master CAD Assembly (#217)
    * Delete V0.2 Master Assembly RC1.f3d
    * Delete V0.2 Master Assembly RC1.zip
    * Update Master CAD Assembly
    Updated master assembly to contain thicker front cowling and reworked skirts.
    Closes issue #212.
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2023-01-19 missing accent name tag (#222)
    [[a]_FS_Creality_Spider_Hotend_Mount.stl, [a]_FS_Hotend_Mount_Dragon.stl, [a]_FS_Hotend_Mount_Dragonfly_BMO.stl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]
2023-01-20 re exported stls to fixed rear bottom panel clips (#225)
    * updated to the correct panel clips for the rear panel
    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
    [Rear_Bottom_Left_Clip_x1.stl, Rear_Bottom_Right_Clip_x1.stl]
2023-01-22 Add files via upload (#227)
    * Delete VORON_V0.2_Assembly_Manual.pdf
    * Create readme.md
    * manual fixes
    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
    [SKR_E3_V3_Din_Mount.STL]
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2023-02-02 Added/Fixed missing controller mounts (#242)
    * added fly gemini and updated skr mini e3 CAD and STLs
    * added Manta M4P din mounts
    [Fly_Gemini_V2_Din_Mount_2pc.step, Fly_Gemini_V2_Din_Mount_2pc.stl, Manta_M4P_Din_Mount_2pc.step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]
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2023-02-08 Change Print End Park Position (#245)
    Move to maxy - 10 in the default print end to allow sensorless homing to work correctly on the next print
    [bigtreetech-manta-m4p.cfg, bigtreetech-skr-3-ez.cfg, bigtreetech-skr-mini-e3-v2.0.cfg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]
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2023-03-29 Macro fix (#266)
    * Update bigtreetech-manta-m4p.cfg
    * Update fysetc-cheetah-v2.0.cfg
    * Update mellow-fly-gemini-v2.cfg
    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
    [bigtreetech-manta-m4p.cfg, bigtreetech-skr-3-ez.cfg, bigtreetech-skr-mini-e3-v2.0.cfg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]
2023-03-29 Fix syntax error in _HOME_Z and remove xy moves (#267)
    [bigtreetech-manta-m4p.cfg, bigtreetech-skr-3-ez.cfg, bigtreetech-skr-mini-e3-v2.0.cfg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]
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2023-04-26 Z home fix (#282)
    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
    [bigtreetech-manta-m4p.cfg, bigtreetech-skr-3-ez.cfg, bigtreetech-skr-mini-e3-v2.0.cfg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]
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2023-06-10 Z endstop missed (#295)
    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
    [[a]_Z_Endstop_Mount_x1.STL, [a]_Z_Endstop_Mount_x1.stl]
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2023-06-14 Fix hartks bowden mess (#299)
    * Delete MiniSB_Bowden_ECAS04.stl
    * Delete MiniSB_Bowden_M10.stl
    * Delete MiniSB_Bowden_M6.stl
    * Delete MiniSB_Cowling_Multibody.stl
    * Delete readme.md
    * cad
    * name
    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
    [MiniSB_Bowden_ECAS04.stl, MiniSB_Bowden_M6.stl]
2023-06-26 Macro 0.7 fix (#305)
    * Upda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
    [bigtreetech-manta-m4p.cfg, bigtreetech-skr-3-ez.cfg, bigtreetech-skr-mini-e3-v2.0.cfg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]
2023-07-05 Bowden toolhead fix (#310)
    Right fan inlet wasnt aligned properly to the fan
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2023-10-19 Fix creality spider hotend mount name (#325)
    * Delete STLs/Toolheads/Hotend_Mounts/Fan_Saver/[a]_FS_Creality_Spider_Hotend_Mount.stl
    ---------
    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
    [[a]_FS_Hotend_Mount_Creality_Spider.stl]
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
